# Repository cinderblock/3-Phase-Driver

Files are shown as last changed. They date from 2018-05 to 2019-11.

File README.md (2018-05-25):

# Tom Sawyer Labs - 3 Phase Motor Driver

This is our open source 3 Phase BLDC motor controller hardware.

This hardware works, but there are many little issues that need fixing.

This design was originally created for our commercial venture **Last Mile Robotics**.
The intention was always to open the source this component of the project. So here it is.

Of course this is presented without any warranty or assurance that this will work.

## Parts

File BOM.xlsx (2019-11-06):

Quantity | Description | RefDes | Package | Min Rating | Manufacturer | Manufacturer Part No. | Digi-Key Part Number
6 | RESISTOR, 1Ω | R20, R21, R24, R25, R28, R29 | IPC-7351\Chip-R0402 | 1/20W 5% |  | CRCW04021R00JNED |  | Alternate OK
4 | RESISTOR, 10Ω | R2, R3, R17, R18 | IPC-7351\Chip-R0402 | 1/20W 5% |  | RK73B1ETTP100J |  | Alternate OK
4 | RESISTOR, 1kΩ | R1, R4, R11, R19 | IPC-7351\Chip-R0402 | 1/20W 5% |  | CRG0402J1K0 |  | Alternate OK
8 | RESISTOR, 10kΩ | R7, R9, R14, R15, R16, R23, R27, R31 | IPC-7351\Chip-R0402 | 1/20W 5% |  | RC1005J103CS |  | Alternate OK
7 | RESISTOR, 100kΩ | R5, R8, R12, R13, R22, R26, R30 | IPC-7351\Chip-R0402 | 1/20W 5% |  | RK73B1ETTP104J |  | Alternate OK
1 | RESISTOR, 140kΩ | R6 | IPC-7351\Chip-R0402 | 1/20W 5% |  | RC0402FR-07140KL |  | Alternate OK
1 | RESISTOR, 3mΩ | R10 | Ultiboard\FCSL64 | 3W 1% |  | KRL6432E-M-R003-F-T1 | 408-1613-1-ND | Alternate OK
2 | CAPACITOR, 12pF 6V | C9, C10 | IPC-7351\Chip-C0402 | 6V |  | C0402C120J8GAC7867 |  | Alternate OK
10 | CAPACITOR, 0.1µF 6V | C5, C6, C11, C17, C18, C19, C20, C21, C23, C24 | IPC-7351\Chip-C0402 | 6V |  | GRM155R71C104KA88J |  | Alternate OK
4 | CAPACITOR, 0.1µF 16V | C12, C25, C32, C39 | IPC-7351\Chip-C0402 | 16V |  | GRM155R71C104KA88J |  | Alternate OK
7 | CAPACITOR, 1µF 6V | C1, C2, C3, C4, C7, C8, C46 | IPC-7351\Chip-C0402 | 6V |  | GRM155C81A105KA12D |  | Alternate OK
3 | CAPACITOR, 1µF 16V | C26, C33, C40 | IPC-7351\Chip-C0603 | 16V |  | C0603C105K4RACTU |  | Alternate OK
2 | CAPACITOR, 10µF 6V | C15, C22 | IPC-7351\Chip-C0603 | 6V |  | GRT188R61E106ME13D |  | Alternate OK
2 | CAPACITOR, 10µF 16V | C14, C16 | IPC-7351\Chip-C0805 | 16V |  | C0805C106K4PACTU |  | Alternate OK
1 | CAPACITOR, 4.7µF 50V | C13 | IPC-7351\Chip-C1206 | 50V |  | C1206C475K5RACTU |  | Alternate OK
6 | CAPACITOR, 10µF 50V | C30, C31, C37, C38, C44, C45 | IPC-7351\Chip-C1206 | 50V |  | GRT31CR61H106ME01L |  | Alternate OK
9 | CAP_ELECTROLIT, 150µF 50V | C27, C28, C29, C34, C35, C36, C41, C42, C43 | Ultiboard\CAPPR350-800X1150 | 50V |  |  | P122400-ND
1 | TVS_DIODE_SMB_ON_Semi_1SMB, 1SMB51AT3G | D1 | ON Semiconductor\DIOM5538X226N |  | ON Semiconductor | 1SMB51AT3G | 1SMB5940BT3GOSCT-ND
5 | Single, 10BQ015 | D2, D3, D4, D7, D10 | Ultiboard\SOD-123F | 1A 50V |  |  | 1655-1928-1-ND | Alternate OK
6 | SCHOTTKY_DIODE, BYS10-45-E3/TR | D5, D6, D8, D9, D11, D12 | Vishay\DO-214AC(DO-214AC) | 3A 50V | Vishay |  | SK310B-LTPMSCT-ND | Alternate OK
1 | INDUCTOR, 22µH | L1 | Ultiboard\VLS5045EX |  |  |  | 445-174849-1-ND | Alternate OK
1 | LED | LED1 | Ultiboard\D0603 |  |  |  | SML-D12U1WT86CT-ND | Alternate OK
6 | POWER_MOS_N, BUK7Y18-75B | Q1, Q2, Q3, Q4, Q5, Q6 | NXP Semiconductors\LFPAK-5(SOT669) |  | NXP Semiconductors |  | 1727-1488-1-ND | Alternate OK
1 | TacSwitch | SW1 | Ultiboard\TL3305 |  |  |  | EG5355CT-ND | Alternate OK
1 | Atmel, ATmega32U4 | U1 | Altera\TQFP-44 |  |  |  | ATMEGA32U4RC-AU-ND
3 | FETDrivers, LM5109 | U13, U14, U15 | IPC-7351\SO-8 |  |  |  | LM5109BMAX/NOPBCT-ND
1 | Isolator, ADUM3160BRWZ | U2 | IPC-7351\SOIC-16W |  | Analog Devices | ADUM3160BRWZ | ADUM3160BRWZ-ND
1 | Buck, AOZ1282 | U3 | IPC-7351\TSOT23-6 |  |  |  | 785-1613-1-ND
1 | LDO, RT9058-50GV | U4 | Zetex\SOT-89 |  |  |  | 497-18286-1-ND
1 | OpAmp, INA181 | U5 | IPC-7351\SOT23-6 |  |  |  | 296-47656-1-ND
1 | OPAMP, MCP6001T-I/OT | U6 | Microchip\SOT-23-5(OT) |  | Microchip |  | MCP6001T-I/OTCT-ND
1 | Interfaces, ISL81487E | U7 | IPC-7351\SOIC-8 |  |  |  | ISL81487EIBZ-TCT-ND
1 | USB | U9 | Ultiboard\1051330011 |  |  |  | WM10134CT-ND
1 | CRYSTAL_SMT_Epson_TSX3225, 16MHz | X1 | Epson Timing\OSCSC230P320X250X80-4N |  | Epson Timing | TSX-3225 16.0000MF09Z-AC0 | SER4069CT-ND
 |  | Do Not Insert
5 | HEADERS_TEST, TEST_PT_SMT | A, B, C, NEG, POS | Generic\TEST_PT_SMT
1 | HEADERS_TEST, HDR1X2 | J1 | Ultiboard\WireToBoard-2
1 | HEADERS_TEST, HDR1X4 | J2 | Ultiboard\WireToBoard-4
1 | HEADERS_TEST, HDR1X6 | J3 | Ultiboard\HDR1x6_EDGE
1 | HEADERS_TEST, HDR1X2 | J4 | Generic\HDR1X2
1 | Ribbon, ISP | ISP | Ultiboard\J-Link 6-pin
4 | SPECIAL, SolderJumper | U8, U10, U11, U12 | Ultiboard\SolderBridge

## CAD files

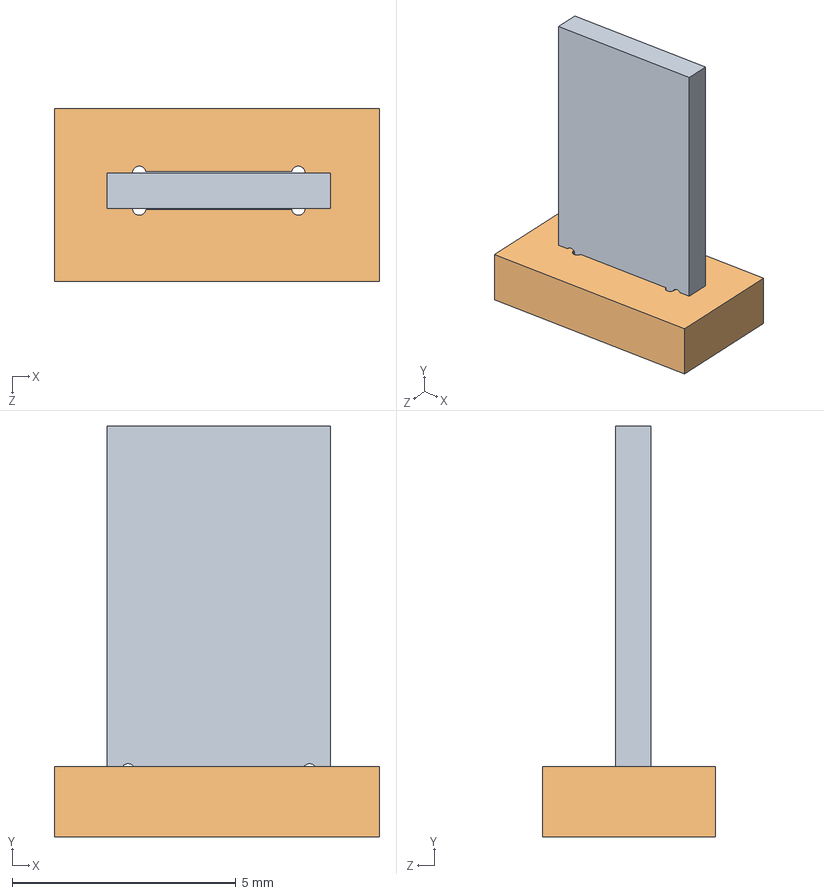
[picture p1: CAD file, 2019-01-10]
Sensor.sldasm
7.28 x 9.19 x 3.87 mm
Sensor
PCB^Sensor

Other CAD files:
Sensor.sldprt

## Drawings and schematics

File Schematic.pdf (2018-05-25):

# CPU

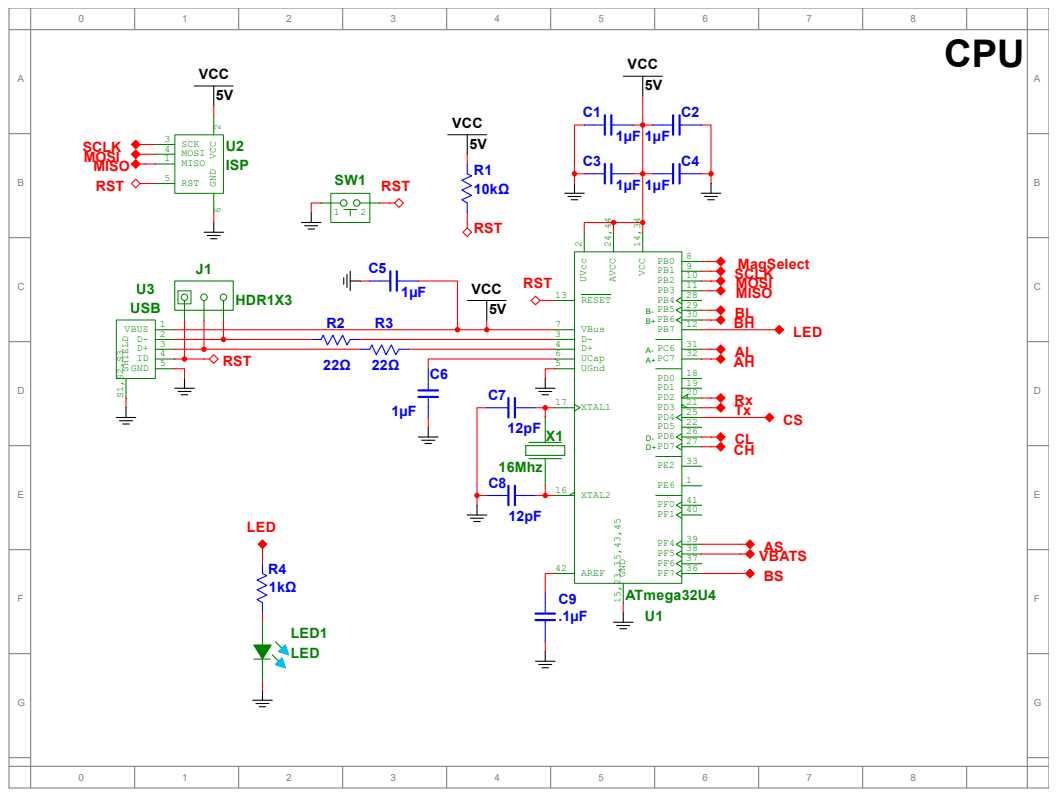
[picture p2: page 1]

MISO MOSI SCLK MagSelect

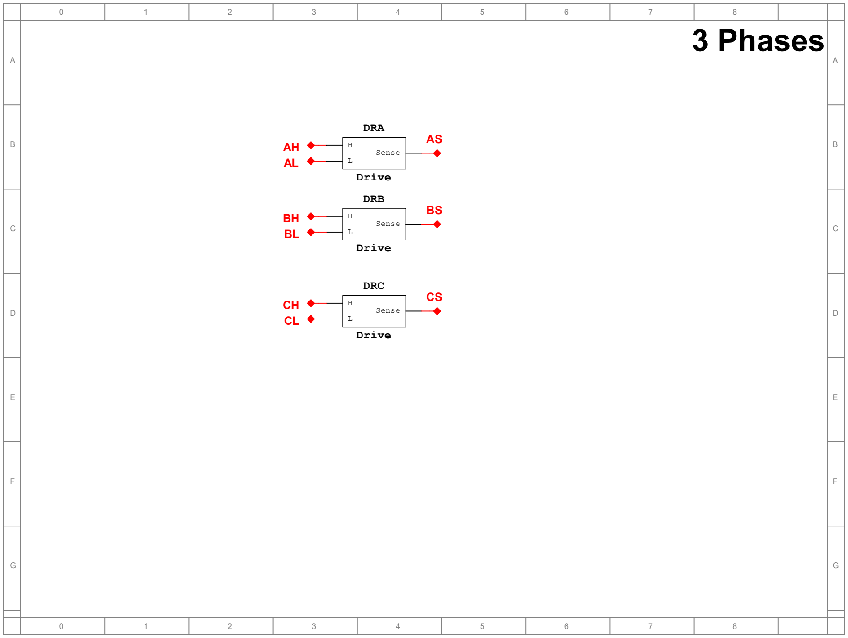
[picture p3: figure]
DRA; Drive; Sense; DRB; DRC; 3 Phases

# Power Supplies

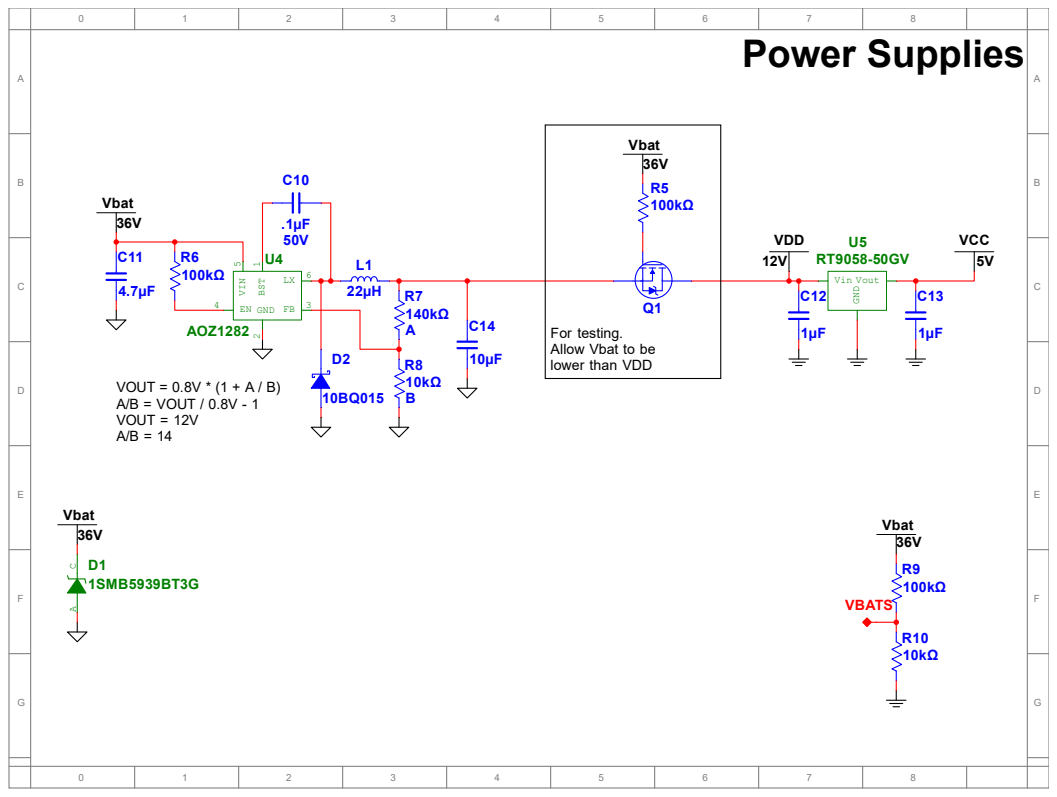
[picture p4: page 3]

For testing.
Allow Vbat to be
lower than VDD

# Sensors

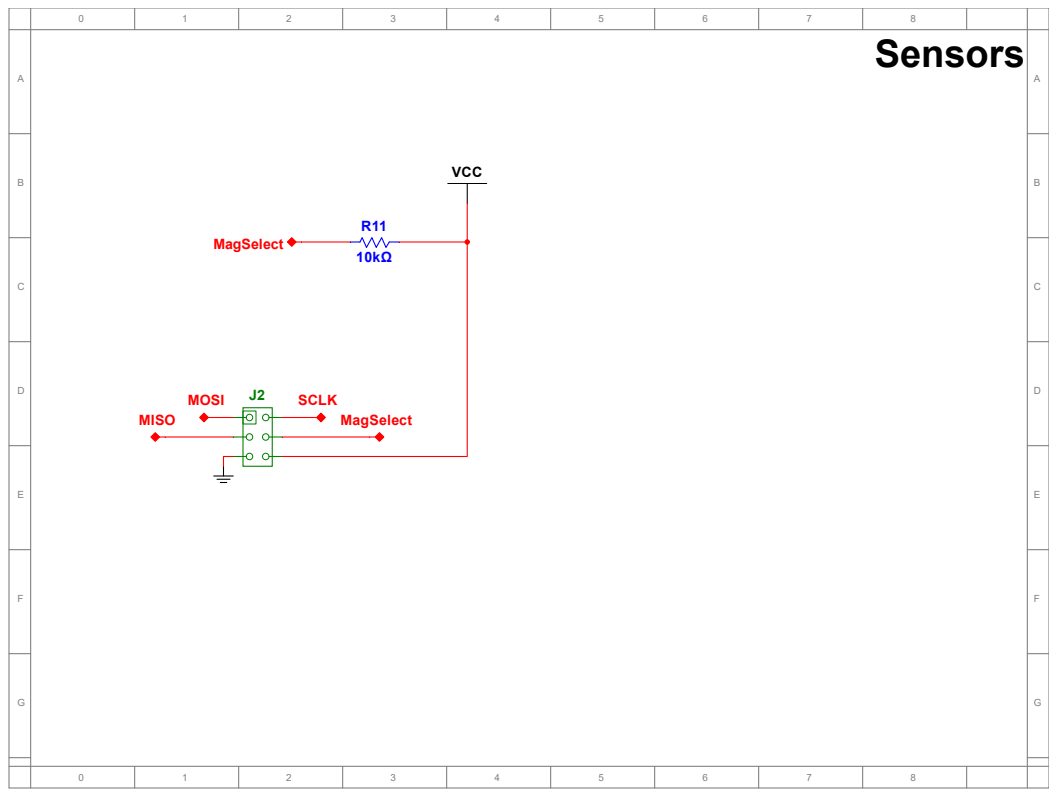
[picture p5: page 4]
MISO; MOSI; SCLK; MagSelect; VCC

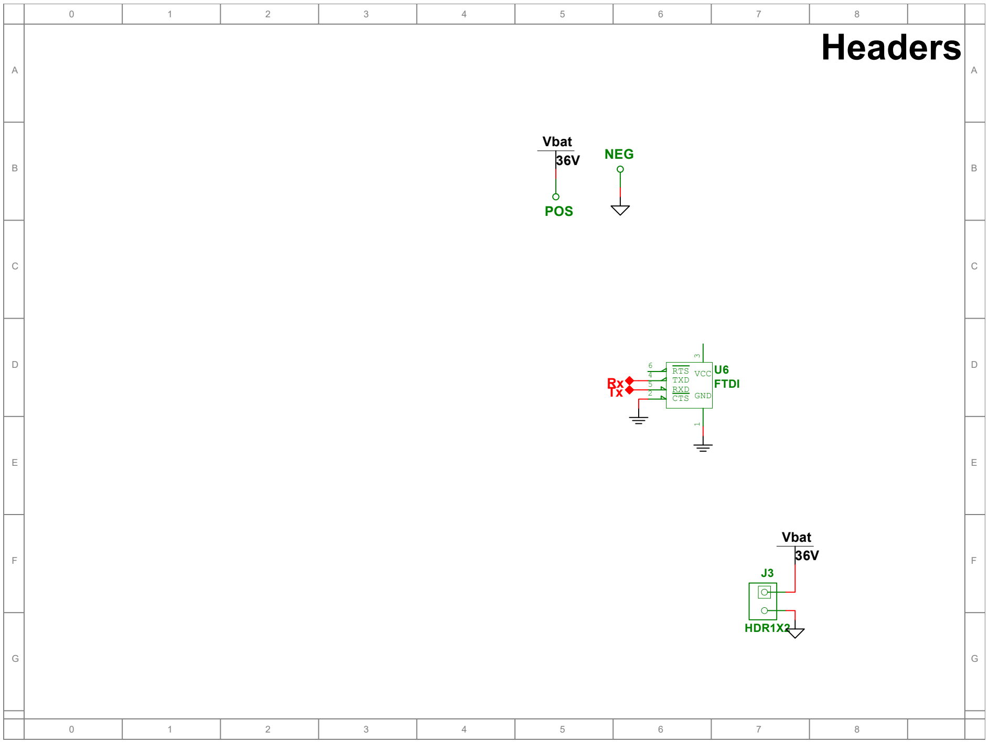
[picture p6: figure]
NEG; POS; Vbat 36V; HDR1X2; U6 FTDI; GND1; CTS ²; VCC³; TXD; 4 RXD ⁵; RTS ⁶; RxTx; Headers

# Half-H

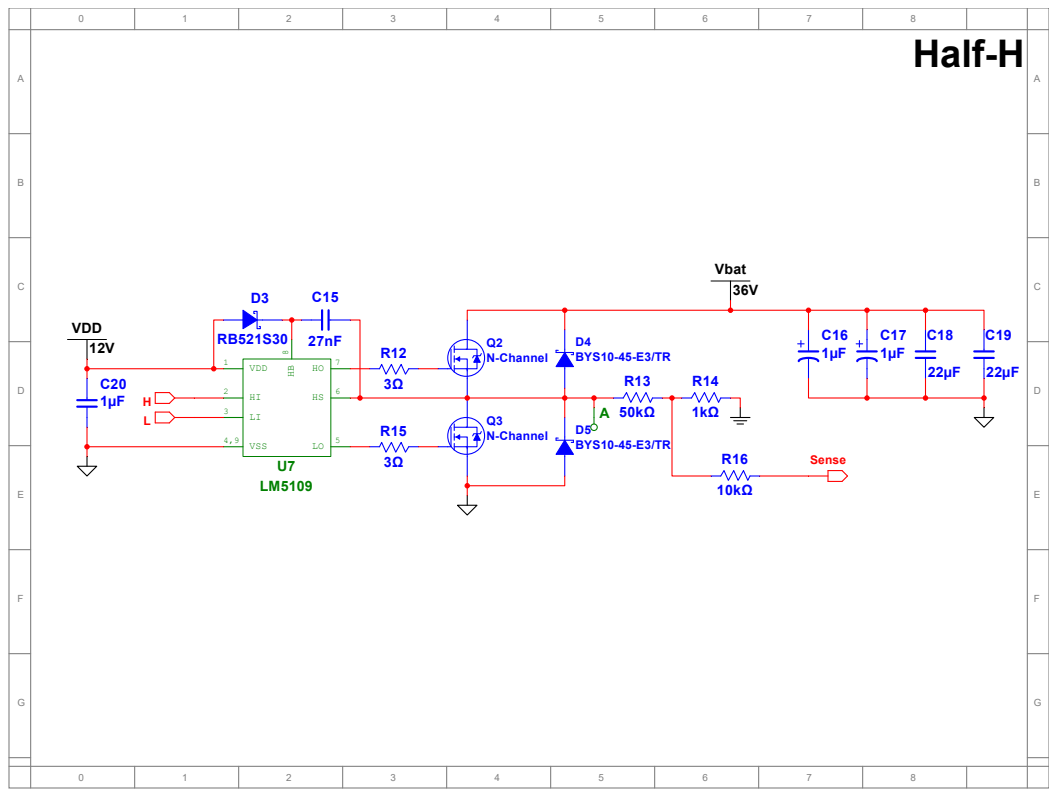
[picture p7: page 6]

# Half-H

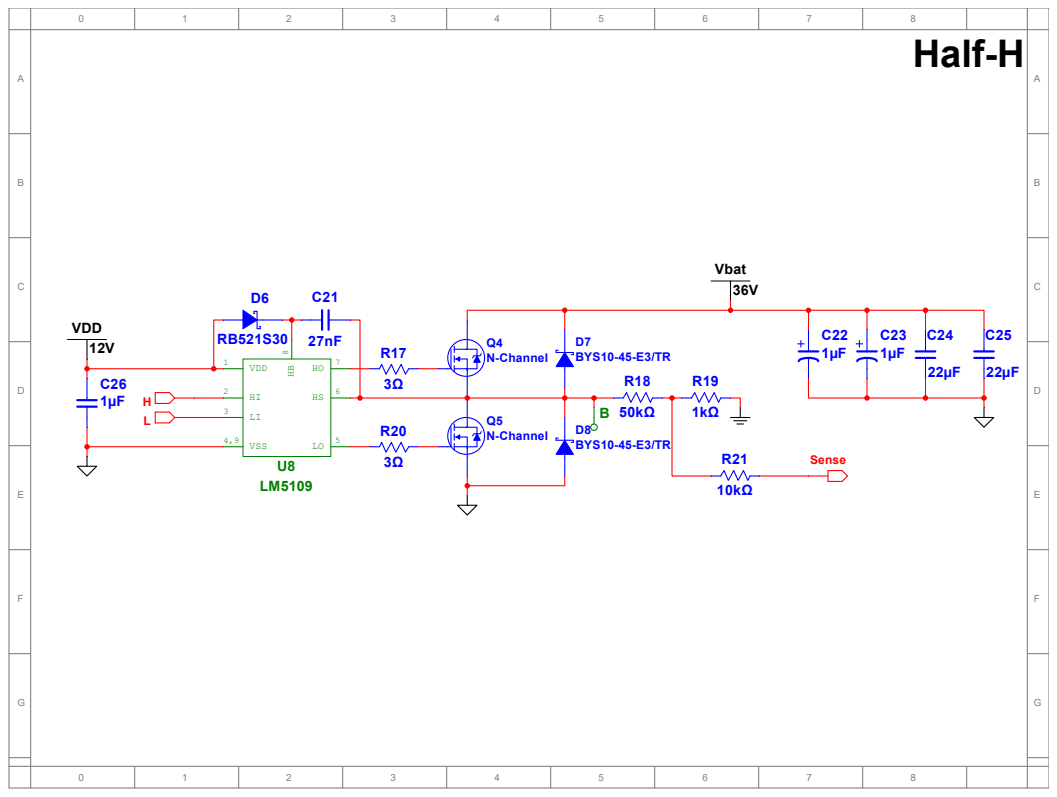
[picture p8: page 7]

# Half-H

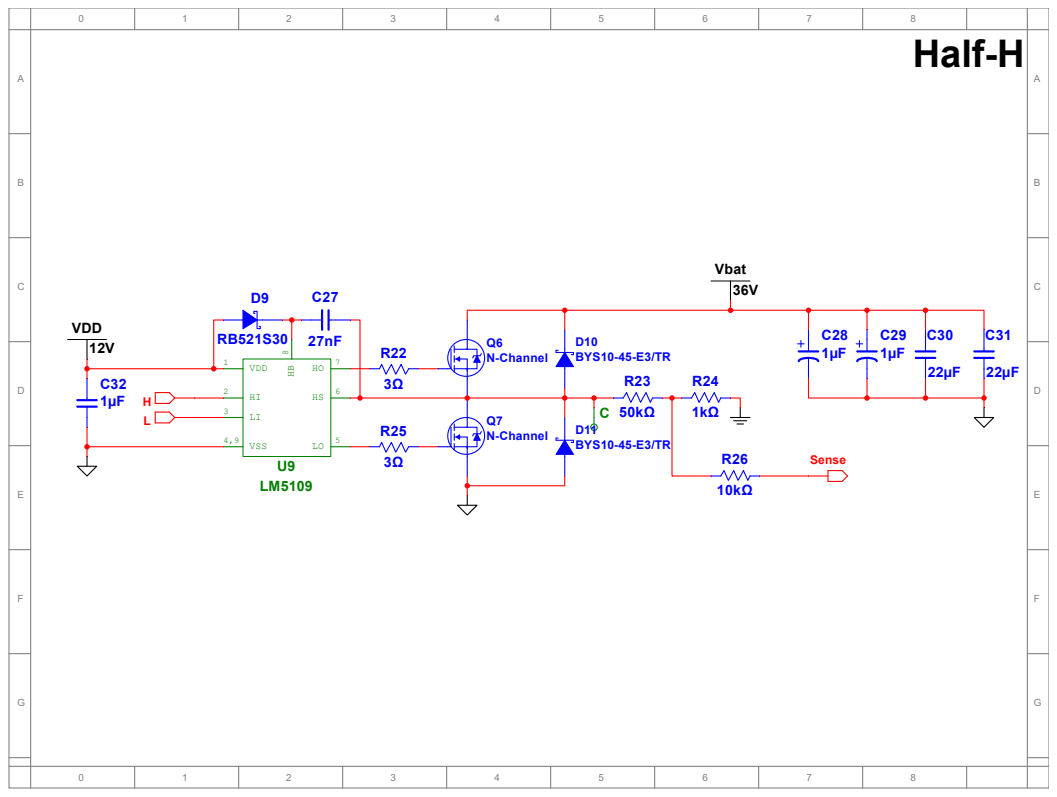
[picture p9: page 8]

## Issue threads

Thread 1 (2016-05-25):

Contribution help

mkapuscik, 2016-05-25:
Could you add a contribution doc outlining real quick how you want the project to work (what layout package you want to use, looks like you are on multisim now right? would you accept contributions of the design ported to a free package like kicad?, etc).

BTW, nice meeting you at makerfaire and sorry about blowing up your controller.

cinderblock, 2016-05-25:
Hey! Was fun to meet you too. I wish I'd realized a 4S pack would blow this up as is. My fault :-/

I'd love to move to something open and free. I just don't have the time to learn it. I'd be glad if the design got converted. I think someone else might already be transferring this to EAGLE. They might want to publish that.

Anyway, high level, I just want to remove the "black magic" aspect of BLDC motor controllers, for the entire chain. If we end up with a (or a few) nice controller design(s) that are useful for the world to be used as is, great.

So, to that end, I'll basically accept any contributions as long as we have a mind to keep things organized and it doesn't devolve to such a crazy collection of things that it's not digestible.

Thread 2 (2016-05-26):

Adding current sensor with fault protection unit support in ATmega32u4

cinderblock, 2016-05-26:
I'm working on version 2 of the ATmega32u4 based PCB. Instead of working on it privately, I'm just going to post my thoughts here.

The main feature I want to add is an aggregate current sensor for all channels. I'm not targeting support for FOC just yet so no need for a per channel measurement. I'd also like to minimize the BOM cost and to that end, ideally use the internal 1/10/40/200x gain amplifier instead of an external instrumentation amp. The main drawback I'm seeing is reduced resolution on the ADC values.

> If 1x, 10x, or 40x gain is used, 8-bit resolution can be expected. If 200x gain is used, 7-bit resolution can be expected.

I'd also like to add support for triggering the built-in fault protection unit in `TIMER4`.

There are two ways to trigger a `TIMER4` fault, `INT0` or the internal comparator output:
> 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

I'd like to use an external comparator to trigger `INT0`. It would allow use of an external resistor resistor divider to set an arbitrary trip point that could be adjusted for different sense resistors or with with an RC-filter off of a separate PWM channel to set a trip point in software.

The other reason to use an external comparator is that we'd like to keep the internal one available for hardware back EMF sensing. The current design allows the output of the ADC multiplexer to use the internal hardware comparator to trigger an interrupt, based off of either the internal 1.1V bandgap reference or an external reference at `AIN0`:
> 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

Unfortunately, my current application uses I2C communications. `SDA` and `INT0` share the same pin and cannot be used in conjunction. Therefore, I need to use the internal comparator as the trigger for `TIMER4`'s Fault Protection Unit and cannot use it for automatic Back EMF sensing. But that's fine since I'm only currently interested in speeds covered by the magnetic shaft sensor's update rate.

If I'm going to use the internal comparator, we'd like to not use an external one. If I connect the top of my current shunt to `AIN0`, I can setup the comparator between that and the 1.1V bandgap reference. Unfortunately, that means a 1.1V drop across the resistor would be needed to trip. Supposing a 30A limit, V = IR, 1.1V / 30A = 37mOhm. But that's also 33Watts (P = VI, 1.1V * 30A = 33W) through that resistor, way to much for the small components I'm hoping to use. For a 1210 resistor, the largest current we could hope to dissipate is 1W, which, at 30A, gives us a .033V signal.

It would be nice to use one for the ADC inputs via the multiplexer to allow setting arbitrary trip values with an external resistor divider. Unfortunately, the ADC multiplexer is in use if we want to use the ADC at all.
> 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
We could choose our inputs such that with the ADC multiplexer settings are correct for both the current sensing ADC and using an external reference to set the fault level on `AIN0`. The downside would be that we couldn't use any of the other ADC channels.

The alternative is to add a single external comparator IC and feed its output to `AIN0`. This would enable the use of other ADC channels. That's a trivial extra part for a good amount of extra flexibility, so I think it's worth it.

For now, I'm also not targeting higher voltage drives. No need to complicate things with a separate gate drive voltage yet.

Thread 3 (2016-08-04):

Battery voltage sensing

misan, 2016-08-04:
It appears that your voltage divider (two 10Kohm resistors) on the battery (12V) side can provide a voltage too high for the 5V 32u4 part. Not sure whether it is a typo on the schematic or that you trust that clamp diode on the controller input pin will take care of that, but it might be a problem.

cinderblock, 2016-08-07:
You are correct, that is wrong. Thanks for pointing it out. It is a result of lazy design. It was one of the things to "figure out" during assembly as exact drive voltage had not been picked during design.

I'd like to start cleaning those little things up. Especially since I'm getting started on V2. Cheers!

mkeyno, 2020-09-13:
@cinderblock are you still working on V2?

mkeyno, 2020-09-13:
@cinderblock are you still working on V2?

cinderblock, 2020-09-13:
@mkeyno I'm on V3~V5 depending on how you count! Some versions of this that I've worked on are unfortunately not going to be made public. However two new versions are published. Checkout the other two branches.

The "Hoverboard" branch is designed to fit the motor controller inside of the common "hoverboard" motors. 2 power wires and 1 USB cable going in gets you a full featured powerful servo motor. The "Quanum" branch is designed to fit onto the back of a specific motor from HobbyKing and interface with a different robot I'm making that we hope to publish soon.

mkeyno, 2020-09-14:
@cinderblock,   I was  wondering whether on open source version there is more information beside the schematic  such as coding or pcb design

cinderblock, 2020-09-15:
@mkeyno, the source files for the PCB are included. Unfortunately the software I use does not include a free viewer, nor is it easy to convert. I have yet to really try switching to a more open software but I'd like to eventually.

The gerbers are also published.

For software, checkout my other repository: https://github.com/cinderblock/3-Phase-Controller

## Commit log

2014-10-09 Import from cad-2
2014-11-03 Switching FETs and their drivers
2014-11-03 Near final schematic. Starting layout. Sexy FET placement. Pre mounting holes.
2014-11-03 Starting to rearrange for new bolt pattern
2014-11-04 Fitting to smaller mounting diameter of motor
2014-11-19 Final FET driver positions. Starting final connections
2014-11-20 VDD Diode. J1. Other stuff
2014-11-21 Near final layout of all components. New debug connectors.
2014-11-22 More routing. New RST button. Removing many DBG headers
2014-11-22 Adding real parts for mounting holes. Potential final programmer placement.
2014-11-22 Most voltage dividers placed
2014-11-24 Some more power vias. VDD plane. cleanup.
2015-10-07 Fixing GND pad orientation on AVR
2015-10-14 Adding pull-up on RST. Taking AVR's SS off of GND. LED 0805 -> 0603. Trace cleanup.
2016-02-26 Hardware layer printouts
2016-02-26 Add schematic
2017-09-28 Simple driver
2018-01-23 Redesign with CPU and FET drivers
2018-05-11 Starting sensor daughter board
2018-05-12 Finished layout. Removed halls and 20-pin. 2 layer. 5/5mil.
2018-05-13 Add sensor board
2018-05-25 Schematic cleanup. Add page labels. Add pdf version of schematic
2018-12-10 Starting rearranging of drivers/MOSFETs to get connections to work
2018-12-27 Updated sensor board design
    [Sensor.sldasm, Sensor.sldprt]
2018-12-27 Use MLX daughter board again
2019-01-07 Intterate on layout some. Submit test slot/sensor pair to PCBWay for test fab.
    [Sensor.sldasm, Sensor.sldprt]
2019-01-10 Fix Test Fit design. All components placed. Main routing done.
    [Sensor.sldasm, Sensor.sldprt]
2019-01-15 New regulator. Rearrange current sense section. Very close
2019-01-16 Update details surrounding slot
2019-05-06 Smaller castellated holes. Increase spacing on 2oz pads.
2019-07-22 WIP. Start of reworking for more motor compatibility
2019-07-22 Just buck left
2019-07-23 Update sensor for 8mm round
2019-07-24 Adding missing solder mask
2019-09-23 Add BOM
    [BOM.xlsx]
2019-11-06 Fixed BOM. Updated files
    [BOM.xlsx]
2019-11-06 Fix silkscreen
